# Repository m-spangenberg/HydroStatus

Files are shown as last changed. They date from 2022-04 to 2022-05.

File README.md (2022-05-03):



<!-- PROJECT LOGO -->
<br />

<div align="center">
  

  <h3 align="center">HYDRO STATUS</h3>

  <p align="center">
    A water usage logger
    <br />
    <a href="https://youtu.be/hqjcAQJdR2c">View Demo Video</a>
  </p>
</div>

</br>

## __Summary__

For my __Harvard CS50__ final project, I set out to create a __hardware application__ that continuously logs mains __water usage__ to a __database__ using a __micro-controller__ and a __flow sensor__. The time-series data is then graphed by a __dashboard__ and monitored by a __notification system__ that sends out __alerts__ when the water usage is too high.

#### __Video Demo__

Hydro Status Demo Video Link (https://youtu.be/hqjcAQJdR2c "Hydro Status Demo Video")

<sub>See the local [demo video](readme/video/hydrostatus_harvardcs50.ogv) if the above link is unavailable</sub>

### __Motivation__

The reason for choosing this project was to help solve a simple problem. I live in a desert climate where water is precious and burst water pipes are a common occurrence, so I set out to find a way to measure and report on our home's water usage to help save water, and reduce water bills. 

### __Features__

The defining features of this project are:

* ♻️ __continuous__: real-time recording and reporting of water usage
* 📊 __metrics__: stores historical usage and and presents it through a dashboard
* 🚨 __notifications__: tracks high usage and sends alerts via a chat application
* 📲 __interactive__: users can query the system for information and set alerts

### __Outcomes__

The scope of the project is guided by the following goals. I will try to work towards reaching these goals within the time I have alloted myself to complete the project and will consider the project a success if I am able to deliver on the 'better' goals.

* __good__:
  * <span style="color:green">\[DONE\]</span> Collect sensor data, push that sensor data to a server hosting a database
  * <span style="color:green">\[DONE\]</span> Read the sensor data from the database and display those metrics on a dashboard
  * <span style="color:green">\[DONE\]</span> Have the system warn the user with a high usage alarm via messaging app
* __better__:
  * <span style="color:green">\[DONE\]</span> Have the system automatically report usage on a weekly and monthly schedule
  * <span style="color:green">\[DONE\]</span> Be able to interactively query the system through a messaging app
  * <span style="color:green">\[DONE\]</span> Have the system passively report its status with a RGB LED
* __best__:
  * <span style="color:green">\[DONE\]</span> Implement a hardware key as basic security
  * <span style="color:orange">\[IN-PROGRESS\]</span> Automate deployment of the software stack with containers
  * <span style="color:orange">\[DESIGNED\]</span> Design a custom breakout board to streamline hardware assembly
  * <span style="color:orange">\[TESTED\]</span> Make the project solar powered but retain continuous, or near real-time operation

<sub>For more information see: <a href="https://cs50.harvard.edu/x/2022/project/">Harvard CS50 final project</a>.</sub>

### __Methodology__

</br>

<div align="center">
  Hydro Status Project Flow
</div>

</br>

I chose to use __InfluxDB__ as the datastore for this project because of how integrated it is in __Grafana__ and well suited it is for time-series data in general. The compiling and flashing of programs to the micro-controller is managed through the __Arduino IDE__. I opted to push sensor data directly from the micro-controller to the locally hosted database using a library called __InfluxDBClient__. The local instance of Grafana, InfluxDB and the __Python notification system__ are hosted as __Docker containers__ on a __Raspberry Pi__ running __Dietpi__, a Linux distribution based on Debian with a small memory footprint.

I decided to use Docker because of ease of deployment. I also make use of __Telegram's Bot API__ and the __Python Telegram Bot library__ to push notifications from the server to the user's mobile device. The notification system makes use of __Requests__ to get __InfluxQL__ queries from the InfluxDB database using the __InfluxDBClient__ library and then transform those queries with __Pandas__ into dataframes that can be plotted by __MatPlotLib__.

---

## __Components__

The following electronic components were sourced for this project:

<div align="center">
  Wiring Diagram
</div>

> Layout needs to be updated: flow sensor no longer requires 5v+ from vn, now runs 3.3v+

* __Micro-Controller__ - 1 X WeMos NodeMCU V3 ESP8266* TTCH340
* __Sensor__ - 1 X YF-B10 Turbine Flow Sensor, DN25, 2-50 L/min, Frequency: 6*Q-8 = l/min
* __Buck-Converter__ - 1 X DC-DC, 12v-5v
* __Photovoltaic Cells__ - 3 X Monocrystalline, in series, 1W 5V, 60x110mm
* __Charge-Controller__ - 1 X XY-L10A, Overcharge Protection, Digital Reporting
* __Battery__ - 1 X Reclaimed, Sealed Lead-Acid, 12v 7aH
* __LED__ - 1 X 10mm Common Anode Diffused RGB LED
* __Ressitors__ - 5 X 100 Ohm resistors

<sub>* See <a href="https://arduino-esp8266.readthedocs.io/">esp8266 documentation</a> and <a href="https://github.com/nodemcu/nodemcu-devkit-v1.0">modemcu-devkit</a> for more information.</sub>

### __Flow Rate Calculations__

To calculate the __Flow Rate__ of the fluid through the sensor we need to read the flow sensors __Pulse Frequency__ and divide those pulses by the sensors __Calibration Factor__.

The calibration factor for this sensor is __6 * Q - 8__. Where __Q__ is flow rate in L/min. The Formula for L/min then is __((pulses + 8) / 6)__. While calibrating the sensor manually, I found __((pulses + 3) / 6)__ gave more accurate results.

```c
flow_rate = ((1000.0 / (millis() - ms_previous)) * (pulses_sec + 3)) / 6;
```

### __Notes__

```md
15-02-22 - I was unable to find 150 Ohm resistors so I put two 100 Ohm resistors in parallel giving me a 50 Ohm resistor and placed this new 50 Ohm resistor in series with a 100 Ohm resistor to make 150 Ohm needed for the red channel of the RGB led to function at 5V+.

01-03-22 - Unfortunately the micro-controller I was using at the start of the project developed an electrical fault, causing a 1N5819 Schottky Diode to fail.

04-03-22 - I have managed to revive the micro-controller by bypassing the Schottky diode. This is a temporary solution until I can get components or a new controller.
```

---

## __InfluxDB Database__

>🟩 STATUS: DONE.

For the database I opted to use a downsampling and retention policy that doesn't put too much stress on the Raspberry Pi's limited memory and CPU cycles. The default policy retains the raw data for a maximum of 1 week after which it resamples the data in order to reduce the number of data points but retain meaningful time series information. 

### __Database Setup__
```sql
# Create admin and password
CREATE USER admin WITH PASSWORD "admin-password" WITH ALL PRIVILEGES

# Create user and password
CREATE USER username WITH PASSWORD "user-password"

# Create database
CREATE DATABASE watermeter

# Grant user privileges on database
GRANT ALL ON watermeter TO username

# Select the database for use
USE watermeter

# Create measurements and tags
# flowrate -- Flow in litres per minute (instantaneous)
# usage -- Usage in litres per second (periodical)
INSERT water,sensor=flowsensor flowrate=0,usage=0
```

### __Create Retention Policies__
```sql
CREATE RETENTION POLICY "retainweek" ON "watermeter" DURATION 1w REPLICATION 1 DEFAULT

CREATE RETENTION POLICY "retainmonth" ON "watermeter" DURATION 4w REPLICATION 1

CREATE RETENTION POLICY "retainhalfyear" ON "watermeter" DURATION 24w REPLICATION 1

CREATE RETENTION POLICY "retainyear" ON "watermeter" DURATION 52w REPLICATION 1
```

### __Create Continuous Queries__
```sql
CREATE CONTINUOUS QUERY "minute" ON "watermeter" BEGIN SELECT sum("usage") AS "1m-usage" INTO "retainmonth"."minute" FROM "water" GROUP BY time(1m) END

CREATE CONTINUOUS QUERY "halfhour" ON "watermeter" BEGIN SELECT sum("usage") AS "30m-usage" INTO "retainhalfyear"."halfhour" FROM "water" GROUP BY time(30m) END

CREATE CONTINUOUS QUERY "hour" ON "watermeter" BEGIN SELECT sum("usage") AS "1h-usage" INTO "retainyear"."hour" FROM "water" GROUP BY time(1h) END
```

### __Test Data__

To generate some initial test data, we can manually enter a few data points, as shown below. I have written two small script, one to simulate household water usage and the other to stream realtime data for testing purposes.

<sub>See [dummydataFill.py](database_tools/dummydataFill.py) and [dummydataStream.py](database_tools/dummydataStream.py). in the `database_tools` folder.</sub>

```sql
INSERT water,sensor=flow flowrate=50,usage=0.833  # sensor maximum sensitivity
INSERT water,sensor=flow flowrate=20,usage=0.333  # average household pressure
INSERT water,sensor=flow flowrate=8,usage=0.133  # low pressure warning
INSERT water,sensor=flow flowrate=2,usage=0.033  # sensor minimum sensitivity
```

### __Checks__

After streaming some data to the database, we can check the results of our retention policies and continuous queries by invoking the following commands. We should now be able to see the successful downsampling of data as laid out in our QC and RP rules.

```sql
SELECT * FROM "retainmonth"."minute" ORDER BY "time" DESC LIMIT 5
SELECT * FROM "retainhalfyear"."halfhour" ORDER BY "time" DESC LIMIT 5
SELECT * FROM "retainyear"."hour" ORDER BY "time" DESC LIMIT 5
```

<sub>These instructions are for [InfluxDB v1.8](https://docs.influxdata.com/influxdb/v1.8/).</sub>
<sub>The language [InfluxQL language specification](https://docs.influxdata.com/influxdb/v1.8/query_language/spec/).</sub>
<sub>More information on InfluxDB's [Python Client](https://influxdb-python.readthedocs.io/en/latest/api-documentation.html).</sub>

---

## __Grafana Dashboard__

>🟩 STATUS: DONE.

I chose grafana to build out a functional, locally hosted dashboard. Some pertinent metrics I focused on are:

</br>

<div align="center">
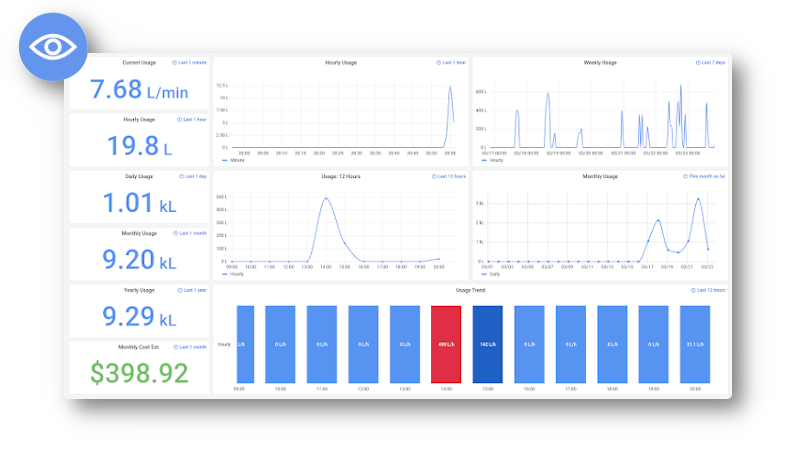
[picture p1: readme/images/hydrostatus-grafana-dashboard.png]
Dashboard
  
</div>

</br>

```md
* Realtime Water Usage
* Total Water Usage (Hourly, Daily, Monthly, Yearly)
* Last 6 Hours Trend Indicating Intensity
* Graphs (Hourly, Daily, Weekly, Monthly)
```

<sub>See [grafana_dashboard.json](resources/grafana_dashboard.json) for the full configuration</sub>

---

## __Reporting & Alerts__

>🟩 STATUS: DONE.

<div align="center">
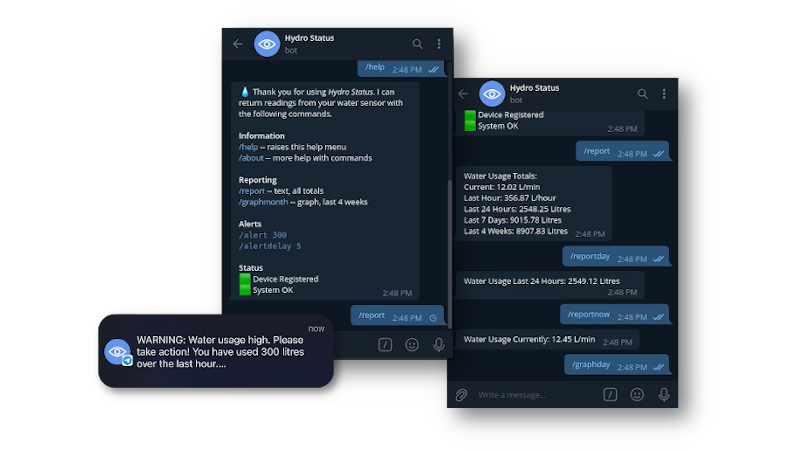
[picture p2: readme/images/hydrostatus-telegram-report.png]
Reporting
  
</div>

</br>

### __Menu__

The notification system relies on a Python application that monitors the database and reports to users via a Telegram Bot when certain alert rules have been met. It also gives users the ability to issue commands to get more information from the bot in an uncomplicated way. To interact with the bot, users can use a forward slash `/` followed by a command. For example: `/help` to get see more options.

| Command | Description |
| --- | --- |
| /start | displays the welcome message |
| /auth | authorizes the device |
| /help | raises the help menu |
| /about | more help with commands |

### __Reports__

The metrics reported are as text and graphs. To get graphs that report usage over time, simply use the `/graph` command immediately followed by either `day`, `week`, or `month` and a corresponding image will be sent to the user. To get a total usage report, simply use the `/report` command or add a modifier like `hour` for a specific time period. See the examples below.

| Command | Description |
| --- | --- |
| /report | all totals |
| /reportnow | last minute total |
| /reporthour | last hour total |
| /reportday | last 24 hours total |
| /reportweek | last 7 days total |
| /reportmonth | last 4 weeks total |
| /graphday | last 24 hours |
| /graphtweek | last 7 days |
| /graphmonth | last 4 weeks |

### __Alerts__

By default the system will notify the user when their water usage exceeds 300L/h for longer than 5 minutes. The defualt should alert the user of a burst pipe even if they have neglected to set the alert. The user can change the existing threshold and delay by issuing the `/alert <litres per hour> <hardwarekey>` and `/alertdelay <minutes> <hardwarekey>` command.

| Command | Description | Limits |  Examples |
| --- | --- | --- | --- |
| /alert| set alert level in litres per hour | min: 180, max: 3000 | `/alert 150 DUMMYKEY` |
| /alertdelay | set alert delay in minutes | min: 1, max: 60 | `/alertdelay 15 DUMMYKEY` |

### __Telegram API Access__

Setting up a Telegram agent to relay notifications only requires the following steps.

```md
1. Open Telegram
2. Search for: BotFather
3. Start a conversation
4. Issue: /newbot
```

See [hydrostatusBot.py](src/hydrostatusBot.py) for more information.

---

## __User Management__

>🟩 STATUS: DONE.

### __Authentication__

Authentication is handled with a simple hardware key tethering the end-user to the hardware. When ownership changes, the new user can simply reauthenticate the device and the hardware will be migrated to the new user's credentials.

#### __Create Tables__

Using `sqlite3` we firs create the database called `hydrostatus.db`, then set up two tables, one called `whitelist` and another called `hardwarekeys`. The hardware keys on every physical device will represent a PRIMARY KEY in `hardwarekeys` which will have an `alert value`, `alert delay` and `user_id` associated with it. Our `whitelist` will contain a list of users and their relation to individual keys in `hardwarekeys`.

```sql
CREATE TABLE hardwarekeys (key varchar(32) primary key, alertvalue real, alertdelay real, user_id varchar(32));

CREATE TABLE whitelist (key varchar(32) primary key, user_id varchar(32));
```

For testing purposes we can set up a dummy hardware key and a dummy user as a placeholder.

```sql
INSERT INTO hardwarekeys(key, alertvalue, alertdelay, user_id) VALUES("DUMMYKEY", 300, 5, 'dummyuser');

INSERT INTO whitelist(key, user_id) VALUES("DUMMYKEY", 'dummyuser');
```

### __Scheduled Reporting__

Users often forget about services until they need them. To keep the user updated about their water consumption it would be good to update them on a weekly or monthly basis without their intervention being needed. A simple approach would be to check the `user_id` linked to a `key` in the `hardwarekeys` table and then have that `user_id` sent a message at the start of every week.

---

## __Enclosure__

>🟩 STATUS: DONE.

The enclosure for this project is a 3D printed electronics assembly housed inside a HDPE tube reclaimed from a caulking gun refill. The tube is plugged with two 3d printed pieces at the top and bottom. The local climate can be quite harsh and the project will have to survive UV exposure, dust, and possible water ingress so a fully 3d printed enclosure out of PLA (available material) would prove to be impractical. I decided to make use of reclaimed HDPE tube from caulking gun refills as these are mildly UV resistant, and often not recycled. Coincidentally, once cleaned, the HDPE tube has translucent properties helping it amplify the status LED. The electronics assembly holds the 5V+ DC power adapter in a jig creating adequate separation between the live and neutral pins and the 220V AC wires powering the supply. It also hold a status LED and the micro-controller board.

<div align="center">
  Enclosure
</div>

<div align="center">
  Enclosure
</div>

---

## __Power System__

>🟩 STATUS: TESTED.

>🟧 NOT USED DUE TO USING MAINS POWER.

The best possible outcome has the project equipment sized for an off-grid installation that runs in a deep-sleep state and wakes in 15-second cycles. Power is supplied by a sealed lead-acid battery being charged by three 5V 1W Monocrystalline photovoltaic cells in series feeding 16.1V (avg) into a programmable charge controller. Intermittent overcast days, conversion losses, and system degradation are factored into the power system sizing. The minimum uninterrupted runtime considered to be a safe is 4 days with the ideal being 7+ days. This is to give a safety margin in case of potential back-to-back overcast days that are possible in the local climate.

#### Power Generation

* __Annual__: *5kWh/y from 3 x 1W cells in series
* __Daily__: *1.64W/h averaged over daylight hours per day

<sub>* estimated using a [solar power calculator](https://pvwatts.nrel.gov/pvwatts.php)</sub>

<!-- > insert chart -->

#### Power Consumption

* wake duration: 10 to 15 seconds for report cycle
* sleep duration: 15 seconds deep-sleep cycle
* consumption:
  * ~48.33 mAh (idle)
  * ~126mAh (reference, wifi scan)
  * ~240mAh (peak, wifi TX)
  * <10mAh (deep-sleep)
* run time: 180 hours assuming a 20% buffer on the 9000mAh battery with 15% losses

---

## __Battery Monitoring__

>🟩 STATUS: TESTED.

>🟧 NOT USED DUE TO USING MAINS POWER.

The charge controller reports battery and charge status over UART. It is possible to read from and write to the controller as long as the correct protocol is used. This allows us to log both battery health and daily solar power generation from the same controller performing the water sensor metering. Through testing I have discovered the battery monitor can potentially introduce a parasitic draw on the system, something to keep in mind.

```md
Protocol: UART
Baudrate: 115200,8,1,
Format: 12.0V,020%,00:10,OP
```

| Command | Description |
| --- | --- |
| on | relay to open state |
| off | relay to close state |
| start | start data reporting |
| stop | stop data reporting |
| read | get parameters of system |
| dw10.0 | set lower limit voltage parameter |
| up20.0 | set upper limit voltage parameter |
| xx:xx | set charging time, 00:00 turns off charge limit |

---

## __Breakout Board__

>🟩 STATUS: DESIGNED.

>🟧 MINOR CHANGE NEEDED: flow sensor no longer requires 5v+ from vn, now runs 3.3v+

As part of my best possible outcome goal, I have put together a design for a prototype breakout board to reduce wiring complexity and to streamline the assembly process. I have never worked with PCBs, or even micro electronics before this point, so I have kept the design simple and only made use of through-hole components.

### Compatible with: __WeMos NodeMCU V3 ESP8266 TTCH340__

</br>

<div align="center">
  Breakout Board
</div>

</br>

```md
* STATUS - Status RGB LED
* FLOW - 3-pin header for Flow Sensor
* DEEP - Toggle switch for Deep Sleep Cycle
* TEMP/BARO - Enclosure Temperature and Humidity Sensor (Optional)
* BATMON - Battery Monitoring from Charge Controller
```

### __Bill Of Materials__

The breakout board needs the following components.

* 2 X 3-pin header, MOLEX, THT
* 1 X Toggle Switch, SPDT, THT
* 2 X Resistor 100Ω, THT
* 1 X Resistor 150Ω, THT
* 1 X RGB LED, Com. Anode, THT
* 1 X (Optional) BMP180 Breakout, GY-68
---

## __Automation__

>🟧 STATUS: BEING IMPLEMENTED.

### __Service Restarts__

Using `crontab -e` we can schedule a task to run at a specified time. For our purposes we want our notification system to have good uptime, but we want to avoid having the system encounter conditions where it might not perform optimally because of memory leaks so we will schedule a daily reboot of the system.

If you're running directly on a host: reboot 15 minutes past midnight and start the service after reboot.
```bash
@daily /sbin/shutdown -r +15
@reboot /usr/bin/python3 /hydrostatus/notifications/hydrostatusBot.py
```

If you're running in a docker container: restart the container at 15 minutes past midnight.
```bash
@daily docker restart <container_name> +15
```

### __Automated Testing__

Unittests

### __Docker__

We can take advantage of containerization by building a Docker image that contains our project and all its dependencies. This will allow us to quickly deploy and test our code across different environments, but the main reason I'm choosing Docker is to take advantage of `Docker Compose` to weave together `InfluxDB` and a `Python environment` for our notification system. This means we build once and deploy anywhere without the steps normally required to manually install and configure each component individually.

#### __Docker Compose__

First we need to set our environment variables. To do that, we copy `.env.sample` to `.env` and set our variables as needed.

```bash
cp src/.env.sample src/.env
```

Then we can use docker-compose to build and run the project. If we push changes to our repo, we can simply do a `git pull` on our server followed by `docker-compose build`, to build a fresh image that's ready for deployment.

```bash
sudo docker-compose build
sudo docker-compose up -d
```

If you run into any restart loops with docker, simply check docker logs using the `--follow` flag or tear down the composed environment and try again.

```bash
sudo docker logs hydrostatus_hydrostatus_1 --follow
sudo docker-compose down -v
```

<sub>See the [docker-compose.yml](docker-compose.yml) for the full configuration</sub>

---

## __Conclusions__

### __Take Away__

I am happy to say that after a month and a half of development and testing my project is finally complete and fully functional. This project allowed me to gain experience with embedded programming, Python scripting, sensor systems, electronics theory, system design, integrating third party services to add value, and much more. I would love to take this concept further and perhaps turn it into a real product if the opportunity presents itself.

### __Future Considerations__

If I were to scale Hydro Status into a multi-tenant service, I would make the following changes:

* Make use of MQTT instead HTTP requests
* Migrate from InfluxDB 1.8 to the InfluxDB 2.0+
* Use Flux scripting language instead of InfluxQL
* Run InfluxDB in a high-availability configuration
* Build custom Docker images and make use of a CI/CD pipeline
* Codebase changes to enable modular services and multiple tenants
* Implement a unique hardware key that tethers access to the device owner
* Migrate from SQLite3 to Postgres for better user management and concurrency

### __License__

Distributed under the MIT License. See `LICENSE.txt` for more information.

### __Acknowledgments__

[Hydro Status](https://github.com/m-spangenberg/hydrostatus) was created by [Marthinus Spangenberg](https://github.com/m-spangenberg) as a Harvard CS50 [project](https://cs50.harvard.edu/x/2022/project/). Thank you to everyone contributing to open source projects and for helping the community build on your hard work to make even more possible. Special thanks to my family and the lifesavers on [Stack Overflow](https://stackoverflow.com/).

The following software, services, and libraries make this project possible.

* [Dietpi](https://dietpi.com/) - Raspberry Pi Operating System (Docker Host)
* [Docker](https://www.docker.com/) - Service Deployment (Docker Containers)
* [Arduino](https://www.arduino.cc/) - C/C++ Micro-Controller Logic (Water Meter)
* [InfluxDBClient](https://github.com/tobiasschuerg/InfluxDB-Client-for-Arduino) - Arduino InfluxDB Library
* [InfluxDB v1.8](https://www.influxdata.com/) - Time-Series Database
* [InfluxDBClient](https://github.com/influxdata/influxdb-client-python) - Python InfluxDB Library
* [Grafana](https://grafana.com/) - Dashboard
* [Telegram API](https://telegram.org/) - Notifications
* [Python Telegram Bot](https://github.com/python-telegram-bot/python-telegram-bot) - Telegram Bot Library
* [Pandas](https://pandas.pydata.org/) - Python Data Manipulation Library
* [Matplotlib](https://matplotlib.org/) - Python Plotting Library
* [Requests](https://docs.python-requests.org/en/latest/) - Python HTTP Library

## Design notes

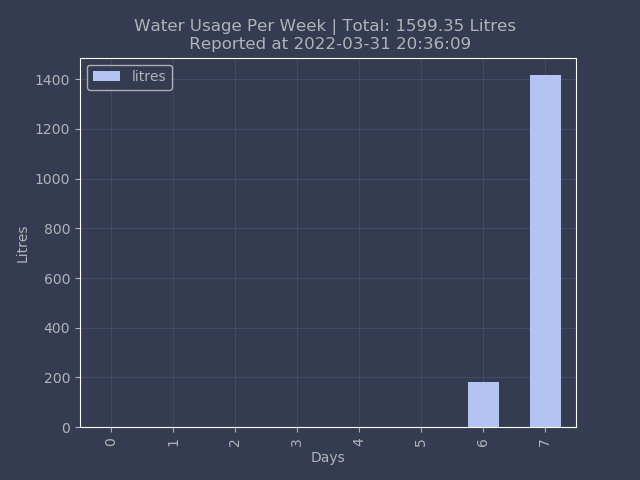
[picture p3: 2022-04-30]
src/graphs/report-week.png

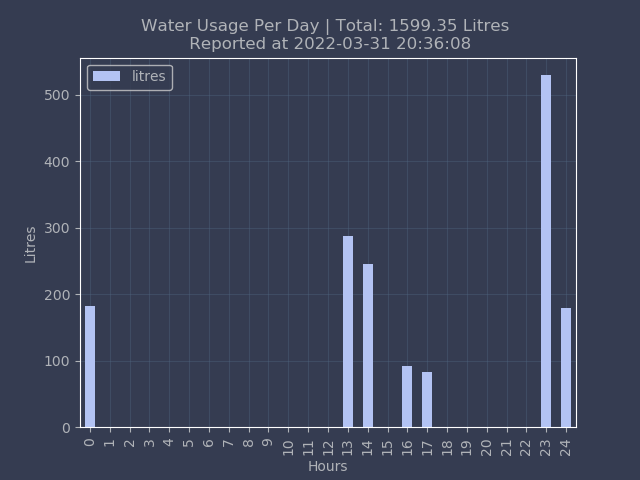
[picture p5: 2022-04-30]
src/graphs/report-day.png

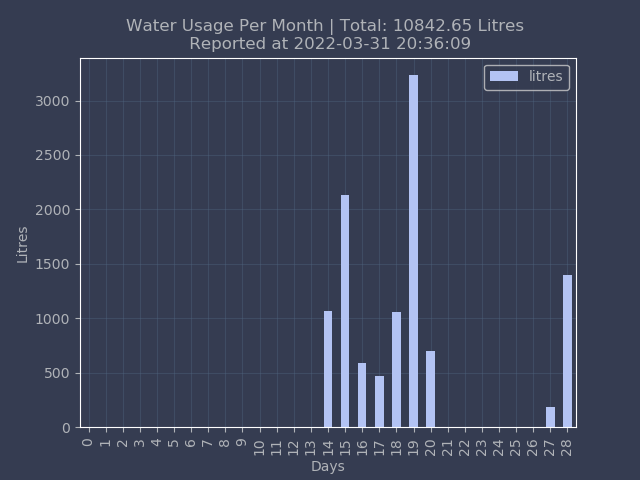
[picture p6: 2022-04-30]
src/graphs/report-month.png

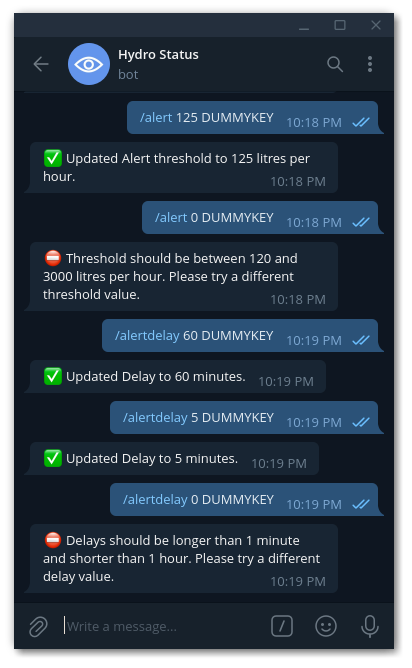
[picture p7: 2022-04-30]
readme/images/Screenshot from 2022-03-30 22-19-32.png

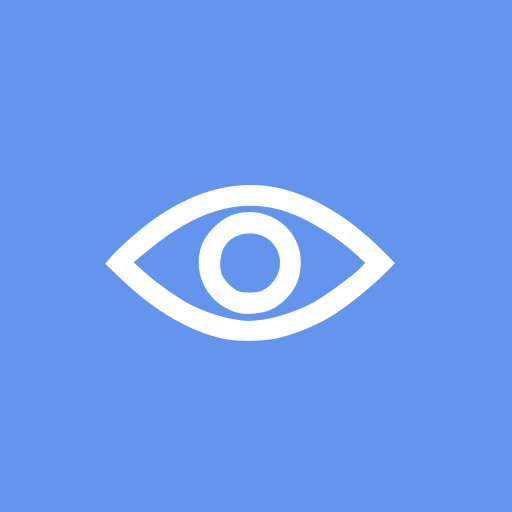
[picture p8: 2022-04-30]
readme/images/hydrostatus-bot.png

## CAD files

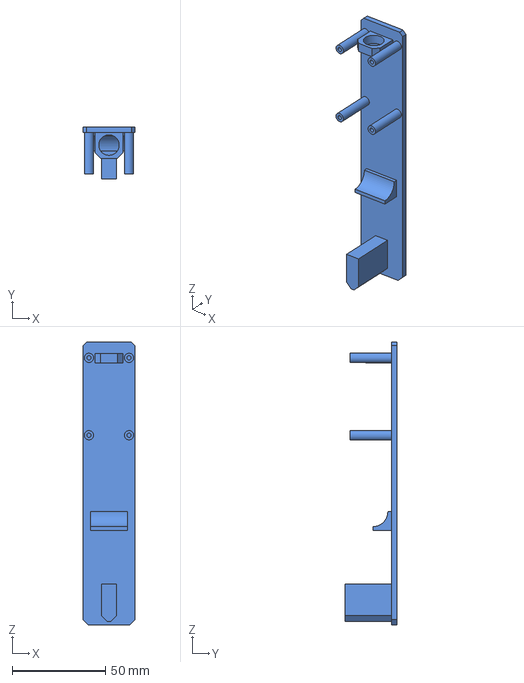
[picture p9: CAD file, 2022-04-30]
enclosure_design/hydrostatus-assembly.FCStd
28.0 x 28.0 x 151.8 mm

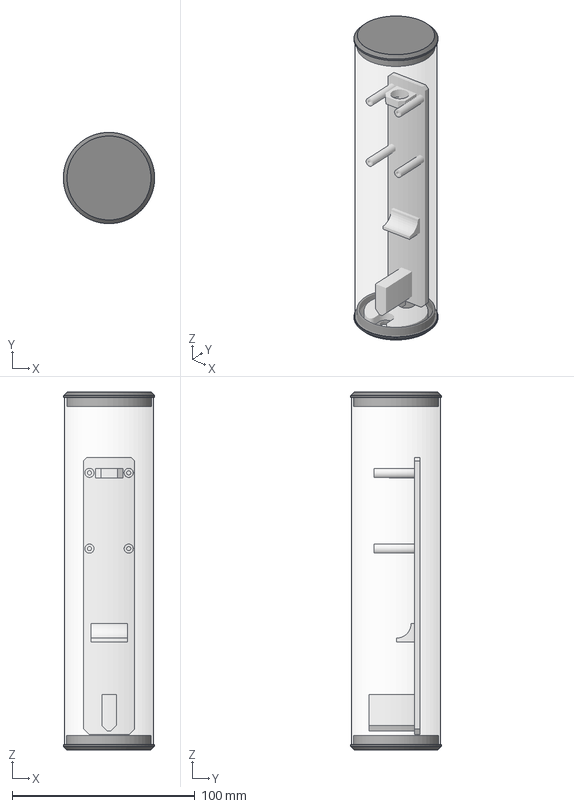
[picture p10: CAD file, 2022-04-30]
enclosure_design/hydrostatus_mockup.FCStd
50.0 x 50.0 x 196.0 mm
hydrostatus_cap
hydrostatus_plug
hydrostatus_tube
hydrostatus_electronics
prototype_layout_refined

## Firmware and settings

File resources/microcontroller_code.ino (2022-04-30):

/*
  Author: Marthinus Spangenberg - https://github.com/m-spangenberg
  Project: Water Meter - https://github.com/m-spangenberg
  
  Micro-Controller: WeMOS NodeMCU V3 with ESP8266
  Sensor: YF-B10 DN25 5V Turbine Flow Sensor
  Status LED: Common Anode Diffused RGB (Resistor Values - R:150R,G:100R,B:100R)
*/

#include <ESP8266WiFi.h>
#include <InfluxDbClient.h>

// Wireless Access
const char* ssid = "INSERTYOURSSID";
const char* pass = "INSERTYOURPASS";
const char* wifi_hostname = "INSERTYOURHOSTNAME";

// Initialize LED pins
#define RED 14  // D5
#define GREEN 12  // D6
#define BLUE 13  // D7

// Initialize Flow Sensor pin
#define SENSOR 4  // D2

// Initialize InfluxDB Credentials
#define INFLUXDB_URL "http://DBIPADDRESS:PORT"
#define INFLUXDB_DATABASE "INSERTYOURDATABASENAME"
#define INFLUXDB_USER "INSERTYOURDBUSER"
#define INFLUXDB_PASS "INSERTYOURDBUSERPASS"

// Initialize Client
InfluxDBClient client(INFLUXDB_URL, INFLUXDB_DATABASE);

// Initialize WiFi Client Library
// See: https://www.arduino.cc/en/Reference/WiFi101SSLClient
WiFiClient ESPclient;

// Initialize Variables
int flashcount = 0;
int flashspeed = 0;

// Initialize Sensor Variables
volatile byte pulse_count;
byte pulses_sec = 0;

// Initialize Flow Calculation Variables
unsigned long ms_current = 0;
unsigned long ms_previous = 0;
int interval = 1000;
float calibration = 6;
float flow_rate;
float flow_litres;
float total_litres;

// Pulse counting function that operates in RAM
void IRAM_ATTR pulse_counter()
{
  pulse_count++;
}

/*
LED STATUS INDICATORS
*/

// Status Indicator LED: Magic

// Status Indicator LED: Breathe
void status_LED_breathe(int flashcount) {
  for(int x=0; x < flashcount; x++) {
    // delay between flashes
    delay(1000);
    
    // set LED to off
    delay(20);
    analogWrite(RED, 255);
    analogWrite(GREEN, 255);
    analogWrite(BLUE, 255);
    
    // breathe in
    for(int i=255; i>0; i--) {
      delay(10);
      analogWrite(RED, i);
      analogWrite(GREEN, i);
      analogWrite(BLUE, i);
    }

    // set LED fully on
    delay(20);
    analogWrite(RED, 0);
    analogWrite(GREEN, 0);
    analogWrite(BLUE, 0);
    

    // breathe out
    for(int i=0; i<255; i++) {
      delay(10);
      analogWrite(RED, i);
      analogWrite(GREEN, i);
      analogWrite(BLUE, i);
    }

    // set LED to fully off
    delay(20);
    analogWrite(RED, 255);
    analogWrite(GREEN, 255);
    analogWrite(BLUE, 255);
  }
}

// Status Indicator LED: Green
void status_LED_green(int flashcount, int flashspeed) {
  for(int x=0; x < flashcount; x++) {
    // delay between flashes
    delay(flashspeed);
    
    // set LED to off
    analogWrite(RED, 255);
    analogWrite(GREEN, 255);
    analogWrite(BLUE, 255);

    // delay between flashes
    delay(flashspeed);

    // set LED to on
    analogWrite(RED, 255);
    analogWrite(GREEN, 0);
    analogWrite(BLUE, 255);
  }
}

// Status Indicator LED: Blue
void status_LED_blue(int flashcount, int flashspeed) {
  for(int x=0; x < flashcount; x++) {
    // delay between flashes
    delay(flashspeed);
    
    // set LED to off
    analogWrite(RED, 255);
    analogWrite(GREEN, 255);
    analogWrite(BLUE, 255);

    // delay between flashes
    delay(flashspeed);

    // set LED to on
    analogWrite(RED, 255);
    analogWrite(GREEN, 255);
    analogWrite(BLUE, 0);
  }
}

// Status Indicator LED: White
void status_LED_white(int flashcount, int flashspeed) {
  for(int x=0; x < flashcount; x++) {
    // delay between flashes
    delay(flashspeed);
    
    // set LED to off
    analogWrite(RED, 255);
    analogWrite(GREEN, 255);
    analogWrite(BLUE, 255);

    // delay between flashes
    delay(flashspeed);

    // set LED to on
    analogWrite(RED, 0);
    analogWrite(GREEN, 0);
    analogWrite(BLUE, 0);
  }
}

// Status Indicator LED: Red
void status_LED_red(int flashcount, int flashspeed) {
  for(int x=0; x < flashcount; x++) {
    // delay between flashes
    delay(flashspeed);
    
    // set LED to off
    analogWrite(RED, 255);
    analogWrite(GREEN, 255);
    analogWrite(BLUE, 255);

    // delay between flashes
    delay(flashspeed);

    // set LED to on
    analogWrite(RED, 0);
    analogWrite(GREEN, 255);
    analogWrite(BLUE, 255);
  }
}

// Status Indicator LED: Ultravoilet
void status_LED_uv(int flashcount, int flashspeed) {
  for(int x=0; x < flashcount; x++) {
    // delay between flashes
    delay(flashspeed);
    
    // set LED to off
    analogWrite(RED, 255);
    analogWrite(GREEN, 255);
    analogWrite(BLUE, 255);

    // delay between flashes
    delay(flashspeed);

    // set LED to on
    analogWrite(RED, 65);
    analogWrite(GREEN, 240);
    analogWrite(BLUE, 20);
  }
}

/*
COMMUNICATIONS
*/

// Wireless
// See: https://arduino-esp8266.readthedocs.io/en/latest/esp8266wifi/readme.html
void connect_wifi() {
  
  int reconnect_count = 0;
  WiFi.hostname(wifi_hostname);

  Serial.print("Device MAC: ");
  Serial.println(WiFi.macAddress());
  Serial.print("Connecting to ");
  Serial.println(ssid);

  WiFi.begin(ssid, pass);

  while (WiFi.status() != WL_CONNECTED) {
    
    // status_LED_uv(2, 100);
    delay(1000);
    reconnect_count ++;

    if (reconnect_count > 20) {
      // status_LED_red(1, 250);
      Serial.println("Trouble connecting...");
    }
  }

  // Confirm Connection
  // status_LED_green(1, 250);
  Serial.println("");
  Serial.println("WiFi connected");
  Serial.println("IP address: ");
  Serial.println(WiFi.localIP());
}

// Serial Debug
void serial_debug() {
  Serial.begin(115200);
  
  // wait for serial connection
  while (!Serial) {
    ; 
  }
  
  Serial.println("");
  Serial.println("Serial connection established...");
  
}

/*
POWER MANAGEMENT
*/

// Power State
// Deep Sleep for 15 seconds, GPIO 16 (D0) <--> RESET
void power_state() {
  Serial.println("Going in deep sleep...");
  ESP.deepSleep(15e6);
}

/*
SENSOR READINGS
*/

// Water Flow
void flow(unsigned long ms_current) {
  
  if (ms_current - ms_previous > interval) {
    pulses_sec = pulse_count;
    pulse_count = 0;

    // Calculate the flow rate per second and the total consumption
    flow_rate = ((1000.0 / (millis() - ms_previous)) * pulses_sec) / calibration;
    ms_previous = millis();
    flow_litres = (flow_rate / 60);
    total_litres += flow_litres;
    
    // Print the flow rate for this second in litres / minute
    Serial.print("Rate: ");
    Serial.print(float(flow_rate));
    Serial.print("L/min ");
    Serial.print(total_litres);
    Serial.print(" Litres Total");
    Serial.println("");

    // Define data point for flow of water in litres per minute
    Point pointDevice("water");
    // Set tags and values
    pointDevice.addTag("sensor", "flowrate");
    pointDevice.addField("value", float(flow_rate));

    // Define data point for usage in litres per second
    Point pointDevice2("water");
    // Set tags and values
    pointDevice2.addTag("sensor", "usage");
    pointDevice2.addField("value", flow_litres);

    // Define data point for total litres flowed since wake cycle
    Point pointDevice3("water");
    // Set tags and values
    pointDevice3.addTag("sensor", "cycletotal");
    pointDevice3.addField("value", total_litres);
    
    // Write data
    client.writePoint(pointDevice);
    client.writePoint(pointDevice2);
    client.writePoint(pointDevice3);
    
  }
}

/*
EXECUTION
*/

// Initialize
// See: https://www.arduino.cc/reference/en/
void setup() {

  // Connect to Serial Console
  serial_debug();
  
  // LED pins
  pinMode(RED, OUTPUT);
  pinMode(GREEN, OUTPUT);
  pinMode(BLUE, OUTPUT);

  // Connect to WiFi
  connect_wifi();

  // Synchronize time with NTP servers and set timezone
  configTzTime("UTC+02", "pool.ntp.org", "time.nis.gov");

  // Disable SSL Certs
  client.setInsecure();
  
  // Configure InfluxDB client
  client.setConnectionParamsV1(INFLUXDB_URL, INFLUXDB_DATABASE, INFLUXDB_USER, INFLUXDB_PASS);

  // Sensor variables
  pulse_count = 0;
  flow_rate = 0.0;
  ms_previous = 0;

  // Measure the SENSOR pin when going from high to low
  attachInterrupt(digitalPinToInterrupt(SENSOR), pulse_counter, FALLING);
  
}

// Tasks
void loop() {

  // Read the sensor
  ms_current = millis();
  flow(ms_current);

}
